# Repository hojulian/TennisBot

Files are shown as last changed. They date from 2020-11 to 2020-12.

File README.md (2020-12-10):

# TennisBot

**Julian Ho, Cass Wang**

**COSI 119A Fall 2020**

TennisBot AR

TennisBot is a tennis playing robot capable of playing a full tennis match.

## Final Report

[Github Pages](https://hojulian.github.io/TennisBot)

## Directory Structure

* `/docs` - final report, github pages
* `/docs/images` - images of the project
* `/firmware` - all firmware/configs for MCU, motor ESCs, and actuator
* `/hardware` - BOM, 3D printed parts files
* `/lib/quickshot` - QuickShot library
* `/models/designs` - 3D design source files
* `/models/gazebo` - 3D models in gazebo
* `/reports` - weekly reports
* `/tools` - snapshot of the tools for ESC configuration

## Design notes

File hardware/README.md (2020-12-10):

# Hardware

## 3D prints

All included STL files are optimized for printing using a Ender 3 V2 printer.

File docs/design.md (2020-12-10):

# Design

TennisBot AR

## Overview

When designing the TennisBot v1, we gave ourselves a couple hard requirements,

1. Capable of shooting a professional shot (~70 mph speed, ~3000 rpm spin)
2. Can shoot a ball to any position of the court, +/- 5cm tolerance
3. Battery powered
4. Portable

With these limitations, we had to constraint and revise our design a lot.

(1) and (2) depends on our motor selection, we needed motors that can reach >10,000 rpm while being relatively lightweight. Therefore we picked a 3548 BLDC motor, which is capable of reaching 19,980 rpm at 22.2v, at 150g a piece. At our maximum requirement of 8500 rpm, this motor will draw ~35A which is acceptable for our use case. In order to accurately land a ball, we need fine control of the shooter's angle. We picked a large 9235 BLDC motor, combined with an AS5047p 14bit absolute magnetic encoder, that gives us a fine grained angle control of 0.02 degrees.

(3) is relatively easy constraint since the modern LiPo batteries can have a high power output while being portable (commonly used in RC cars and drones). We designed the whole robot to be DC powered, and can be charged with a portable power adapter.

(4) created constraint on the physical weight and size of the robot. We designed the robot to have a small footprint (less than the size of a pizza box), and light enough to be carried with a suitcase (~ 10Kg total).

## Changes along the way

During the physical testing of our design, we realized a couple things that needed to be changed.

* Actuator not powerful enough to hold shooter's angle
  * Solution: changed motor from 7032 to a larger 9235
* Belt is too loss/shaky during operation
  * Solution: added 2 idlers, 1 for each motors
* Belt sometimes scratches the carbon fiber plate
  * Solution: changed to narrower belts (12mm -> 10mm width) and also a narrower gear to keep the belt in position (Idlers helped with this as well)
* Not enough friction between the 2 wheels and the tennis ball
  * Solution: changed to larger wheels (83mm -> 90mm diameter) to have a larger contact area with the ball, and compress the ball more during shots
* Encoder producing noisy signal
  * Solution: used shielded cables instead to protect the signal from motors' EMI

## 3D Modelling

TennisBot is designed using Shapr3D. All the source design files can be found under [/models/designs](../models/designs).

Here are some images of TennisBot v1 in 3D and AR.

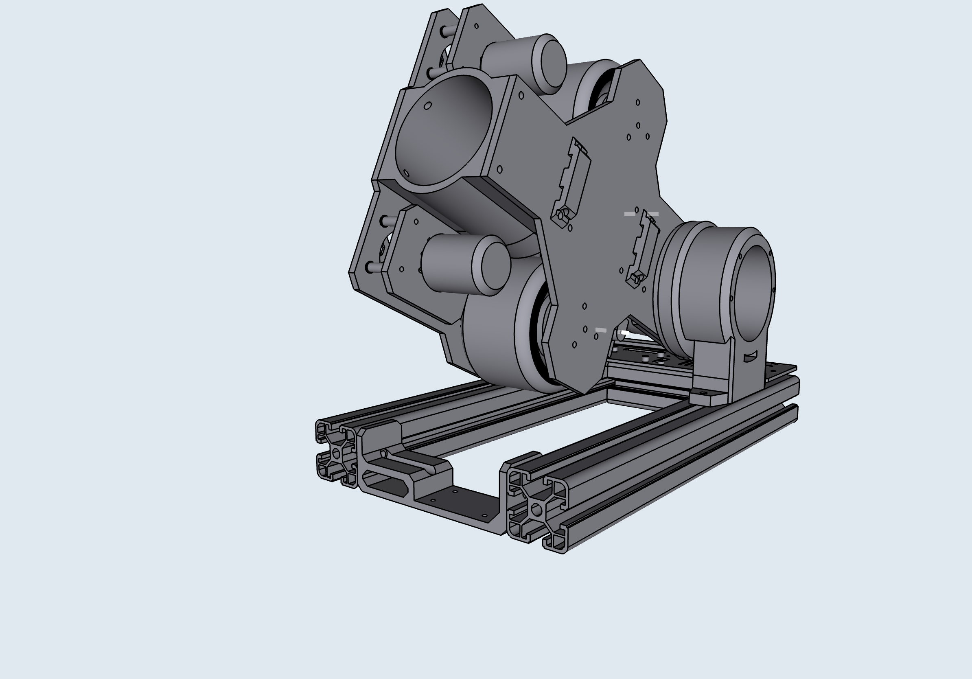
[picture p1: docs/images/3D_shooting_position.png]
3D shooting position


*Shooter at 30 degrees shooting position*

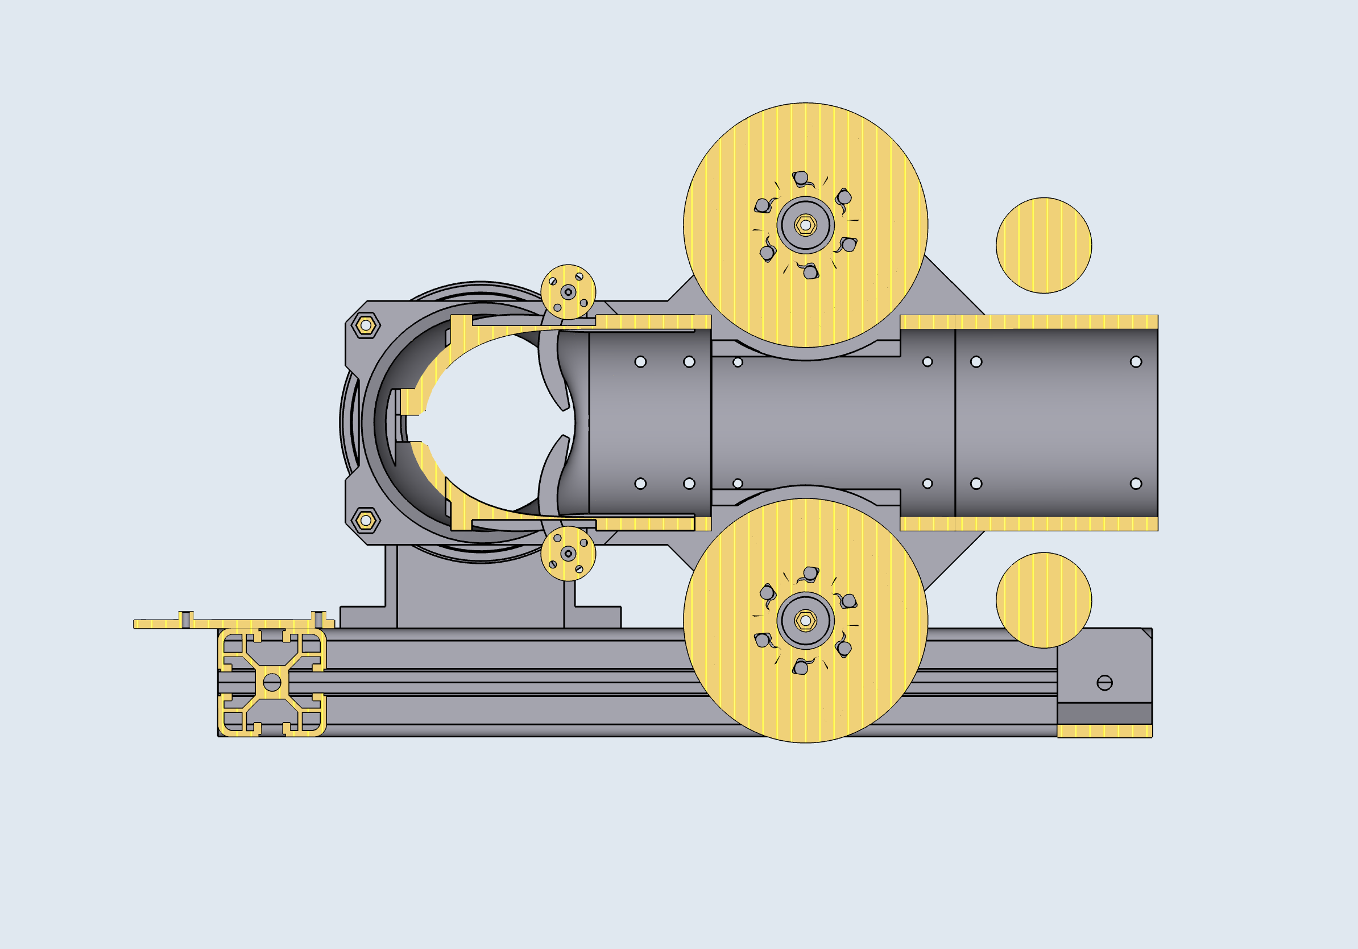
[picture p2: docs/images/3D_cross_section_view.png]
3D cross section


*Cross section of the shooter pipe*

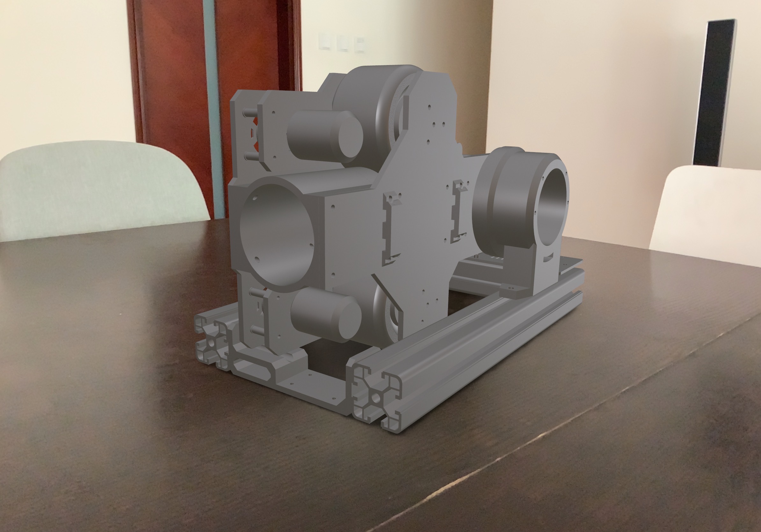
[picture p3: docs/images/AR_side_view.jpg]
AR side view


*Apple AR view*

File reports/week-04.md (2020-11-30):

# TennisBot - Week 4 report

Julian Ho, Cass Wang

## In progress

* Implement firmware for driving tennis shooter hardware using ESP32 (Julian)
* Continue testing URDF implementation in Gazebo (Julian)
* Standardize/clean up ball shooting python library (Cass)

## Completed

* Hardware assembly of the tennis shooter (Julian)
* Initial implementation of the ball shooting library (Cass)

## Planned for next week

* Test out ball shooting library in Gazebo (Julian)
* Building the tennis court in Gazebo (Cass)

## Demo

* Ball launching with dual motors

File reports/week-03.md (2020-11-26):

# TennisBot - Week 3 report

Julian Ho, Cass Wang

## In Progress

* Implement ball shooting algorithms in Python (Cass)
* Test URDF in gazebo and add controls (Julian)
* Building a tennis court in gazebo (Cass)

## Completed

* Convert tennis shooter into URDF (Julian)
* 3D print components to check fit and finish (Julian)

## Planned for next week

* URDF Testing (Julian)
* Finish implementation of ball shooting algorithms in Python (Cass)

## Demo

* Trigger control
* Working URDF model in gazebo

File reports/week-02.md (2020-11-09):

# TennisBot - Week 2 report

Julian Ho, Cass Wang

## In Progress

* Convert tennis shooter into URDF (Julian)
* 3D print components to check fit and finish (Julian)
* Building a tennis court in gazebo (Cass)

## Completed

* Finalize tennis shooter 3D design (Julian)
* Create github repo for the project (Julian)
* Research for ball shooting algorithms (Cass)

## Planned for next week

* Continue building tennis court in gazebo (Cass)
* Convert tennis shooter into URDF (Julian)
* Demo the trigger part of the tennis shooter (Julian)

## Demo

* 3D printed components of the tennis shooter
* Tennis shooter in AR

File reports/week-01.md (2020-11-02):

# Week 1 report

## In Progress

* Finalizing the ball shooter assembly in 3D (Julian)
* Research for building out a tennis court in Gazebo (Cass)

## Completed

* Create github repo for the project (Julian)
* Research for ball shooting algorithms (Cass)

## Planned for next week

* Start building a tennis court in Gazebo (Cass)
* Convert ball shooter assembly to URDF (Julian)

## Demo

* First draft of the TennisBot in 3D
* A [paper](http://www.actawm.pb.edu.pl/volume/vol5no4/WOJCICKI_KULESZA_PUCILOWSKI_EN_2010_085.pdf) regarding ball shooter calculations for ball shooter

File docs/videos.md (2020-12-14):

# Video Demos

* [3D overview](https://drive.google.com/file/d/1ATR15ysar9NvpiEGBQoBEaimcxwtdzJY/view?usp=sharing)
* [Motors control]()
* [Actuator control](https://drive.google.com/file/d/1KERbm8YpcWQQ3XklB0WpKhzmQzhS0fMN/view?usp=sharing)
* [Tennis Court in gazebo](https://drive.google.com/file/d/1kdG3kgPG80MRxjjYmwbdfLqyGcjW15ck/view?usp=sharing)
* [TennisBot V1 in RViz](https://drive.google.com/file/d/1K_xSpBqOkkCilqj5o8Mh0_ldypU9PAPF/view?usp=sharing)

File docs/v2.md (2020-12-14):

# V2 and Beyond

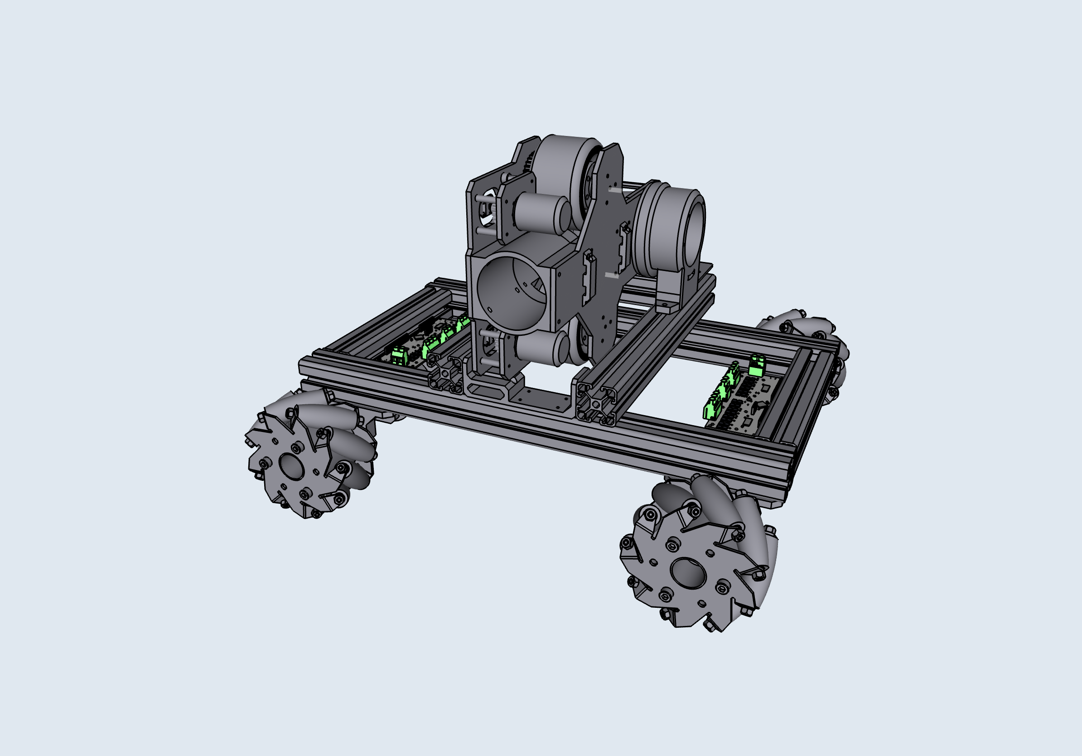
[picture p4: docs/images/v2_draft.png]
TennisBot v2 Draft


The eventual goal for this project is to have a fully automated robot for playing a full tennis match.

## V2 Changes

* A chassis will be added, driven by 4 omni-directional wheels each with an individual motor.
* QuickShot library will support target in `x` direction as well.

    ```python
    # Shoot the ball 1 meter to the left and 2 meters up front.
    q.calc_params(
      y=200,
      x=-100,
      # ...
    )
    ```

* A stereo depth camera on-board for trajectory prediction, in order for the robot to "return" the ball.
* The v2 robot does not actually return the ball in the traditional sense, instead, it moves to where the ball is suppose to land and shoots a ball back immediately.

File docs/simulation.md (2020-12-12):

# Simulation

In order to test out the robot, we exported the 3D model into gazebo, along with a custom built testing ground.

All source files are in [/models/gazebo](../models/gazebo).

## TennisBot v1

In order to keep our simulation simple and smooth, we exported a simplified version of the TennisBot using solidworks' URDF exporter. This simplified verion has a simple geometry while maintaining the exact dimensions of the robot.

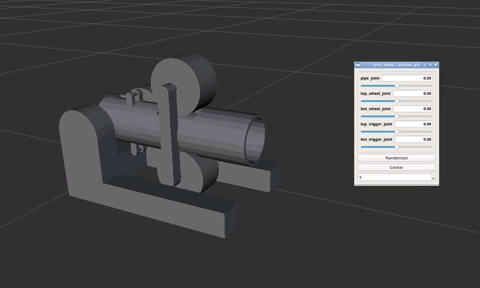
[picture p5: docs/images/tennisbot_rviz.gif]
tennisbot rviz


*^Here it is running in RViz*

This model has a total of 5 joints,

* 1 joint for tilt control
* 1 joint per wheel
* 1 joint per trigger

Each joint can be independently controlled (as shown above).

All the source files can be found in [/models/gazebo/tennisbot_support](../models/gazebo/tennisbot_support).

### Launch in RViz

```bash
roslaunch tennisbot_support display.launch
```

### Launch in Gazebo

```bash
roslaunch tennisbot_support gazebo.launch
```

## Tennis Court

In order to test out our robot design, we first created a tennis court in Blender, then exported it to URDF for use in gazebo.

tennis court blender

*^The red object is our robot*

### Gazebo world

```bash
/models/gazebo/tennis court/Tennis_Court.world
```

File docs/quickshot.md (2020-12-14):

# QuickShot - Tennis Shooting Algorithm

We have created a Python library (QuickShot) for calculating the exact parameters needed for landing a ball to a given location at a given speed/spin using TennisBot v1.

All the calculations/equations here are modified based on this [paper](http://www.actawm.pb.edu.pl/volume/vol5no4/WOJCICKI_KULESZA_PUCILOWSKI_EN_2010_085.pdf).

Our detailed explanations of the implementation of the paper [here](shooting_algorithm.pdf).

## Usage

```python
# Initiate shooter with the robot's physical capabilities
q = quickshot.Shooter(
  min_rpm=400,
  max_rpm=8400,
  min_angle=0,  # min/max angle in degrees
  max_angle=80,
)

# Calculate the parameters needed for shooting the ball.
params = q.calc_params(
  y=200,  # distance (cm) from the robot
  speed=20,  # speed in meters per second
  top_spin=0, # top/back spin in meters per second
  back_spin=0,
)

# Prepare the shooter (spinning up the motors) for the shot.
shooter.prepare(
  top=params['top_motor'],
  bottom=params['bottom_motor'],
  angle=params['angle'],
)

shooter.shot_once_ready()
```

All the source code for QuickShot is located in [/lib/quickshot](../lib/quickshot).

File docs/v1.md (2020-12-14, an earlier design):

# TennisBot v1

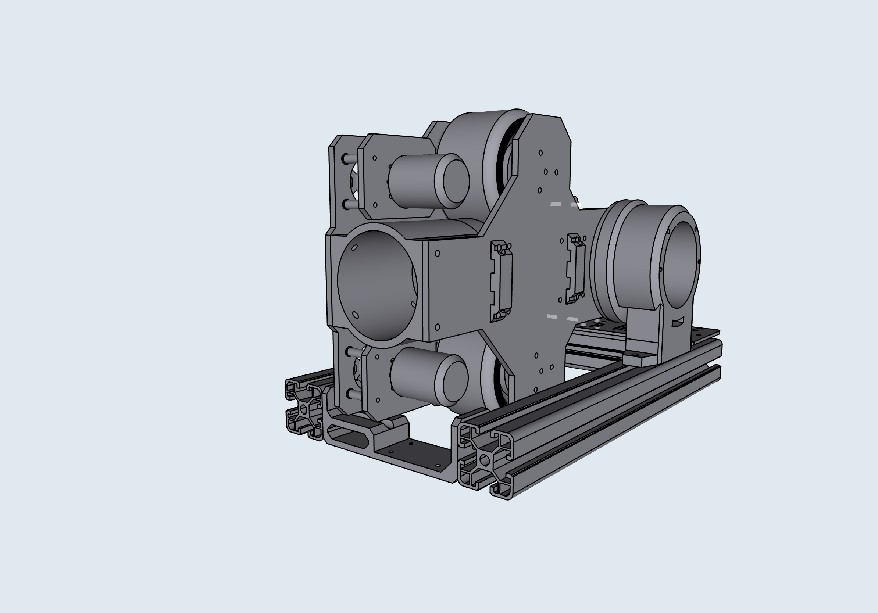
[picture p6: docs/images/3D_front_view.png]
TennisBot v1


TennisBot v1 is a tennis playing robot that can serve balls at a fixed location. It has tilt, top/back spin, as well as ball frequency control. It is capable of shooting the ball at 40 m/s^ (or 89.5 mph) and spin of 8490 rpm^.

*^Theoretical highest speed, based on the selected motor and power output*

## Features

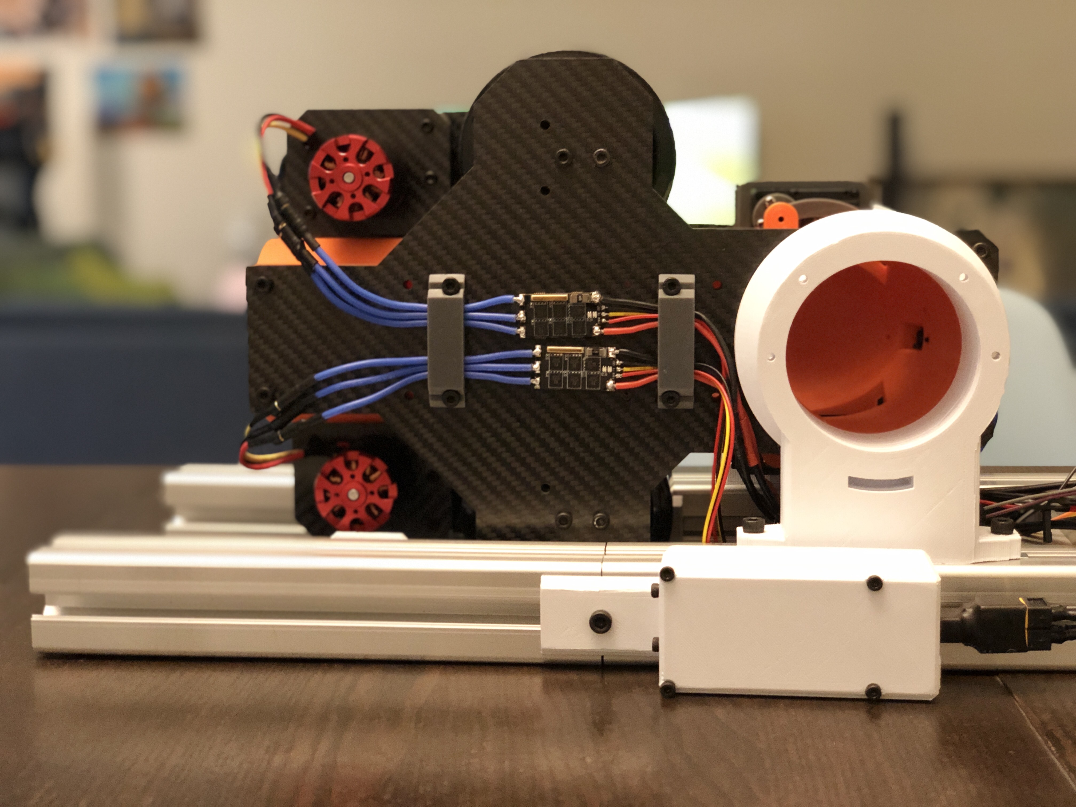
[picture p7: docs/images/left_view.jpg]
Left view


* 40 m/s top ball speed
* 8490 max ball RPM
* battery powered

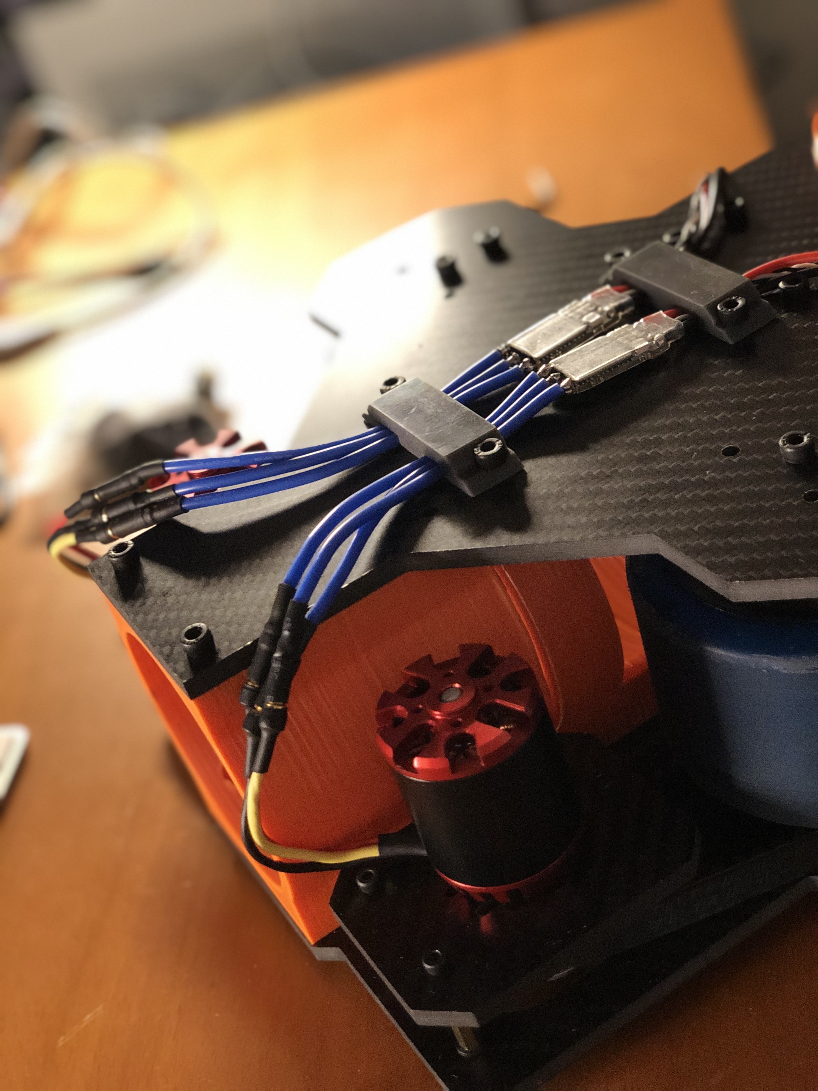
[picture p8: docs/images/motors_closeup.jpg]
Motors closeup


* 2 BLDC motors powered by 2 lightweight ESCs
* 1670W of raw motor power
* 2:1 gear ratio
* 90mm wheels

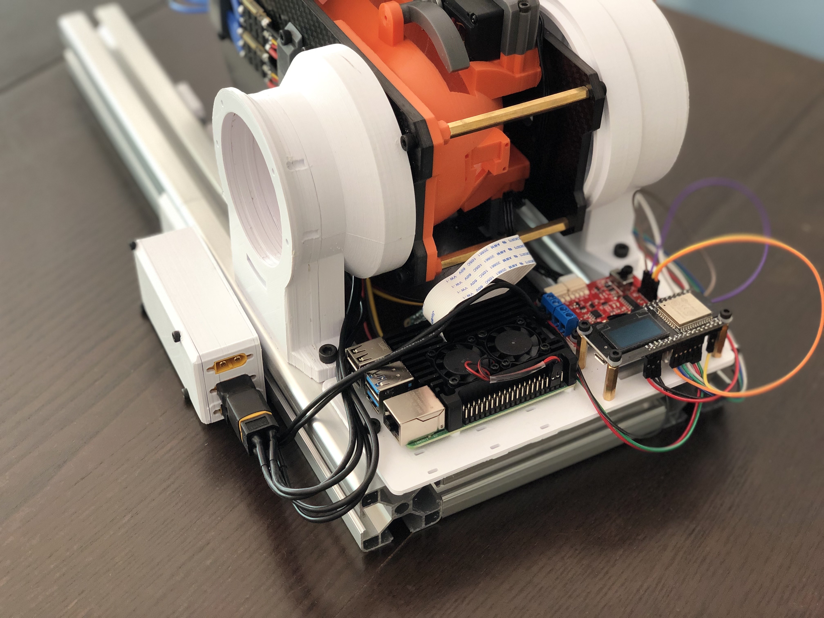
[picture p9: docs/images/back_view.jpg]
Back view


* RPi 4 running ROS melodic
* ESP32 for hardware control
* Communicate using over serial via USB using rosserial

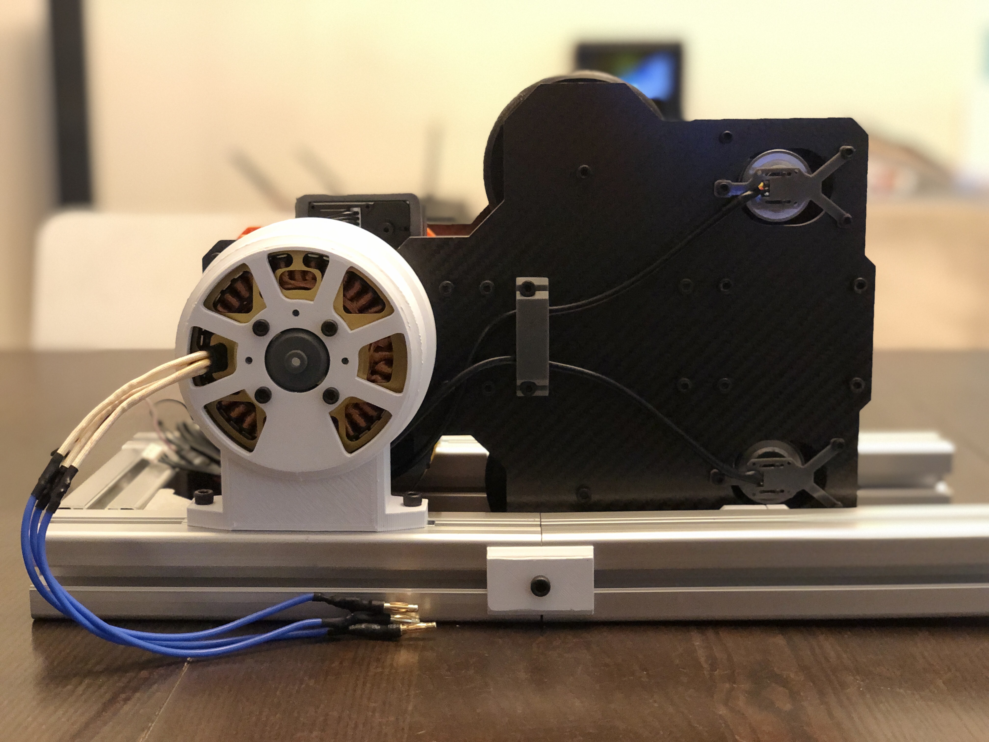
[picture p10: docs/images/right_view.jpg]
Right view


* Dual 14bit magnetic encoders (for RPM tracking)

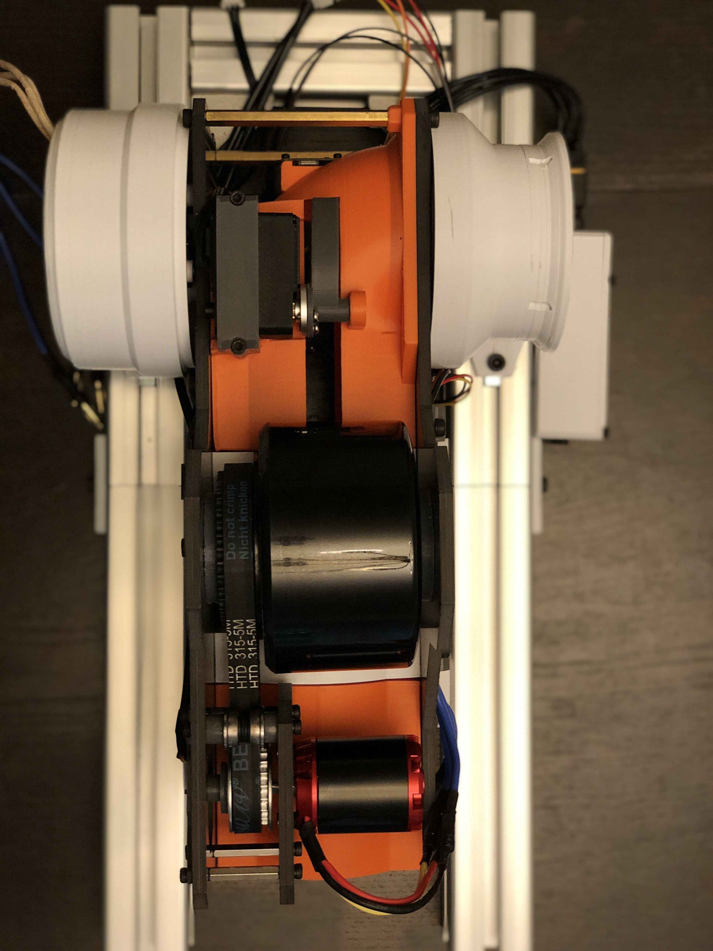
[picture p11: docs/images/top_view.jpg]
Top view


* Belt driven drive
* 2:1 reduction ratio
* Idler for better stability at high RPM

## Design

See [Design](design.md).

## V1 Limitations

This version of TennisBot is not capable of playing a full tennis match just yet, since it only includes the shooter component. However, the shooter component allows us to practice returns, and some tennis drills.

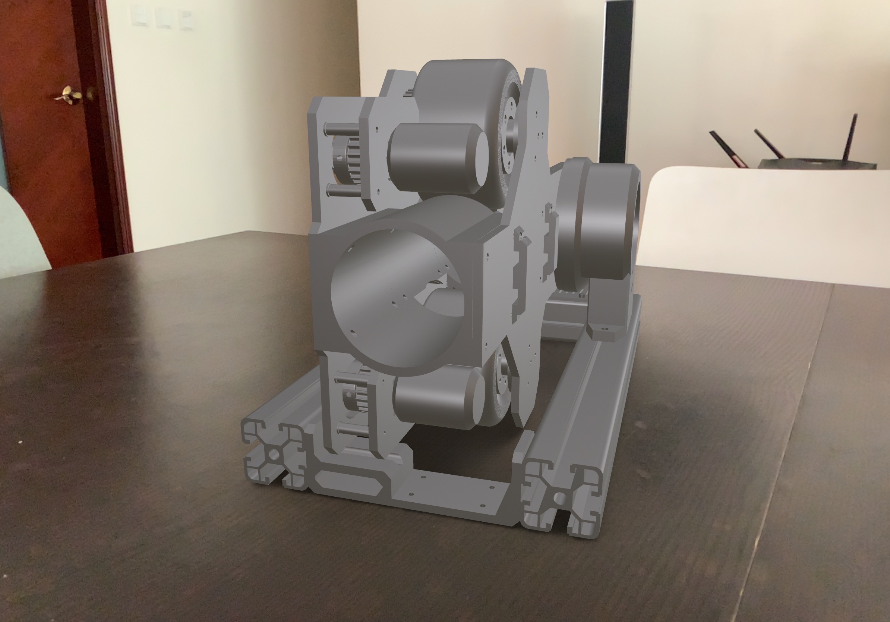
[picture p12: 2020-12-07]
docs/images/AR_front_view.jpg

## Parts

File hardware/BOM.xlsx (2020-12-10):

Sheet: TennisBot v1
TennisBot v1
Product Name | Quantity | Unit Price in USD (As of Nov '20) | Total
ST3215 Servo | 2 | $13.50 | $27.00
URT-1 servo control board | 1 | $6.00 | $6.00
Wraith32 V2 BLDC Controller | 2 | $15.75 | $31.50
N3548 900KV BLDC motor | 2 | $12.94 | $25.87
W9235 BLDC motor | 1 | $25.50 | $25.50
Odrive 3.6 56V BLDC controller | 1 | $69.00 | $69.00
AS5047P encoder | 1 | $9.90 | $9.90
AS5048A encoder | 2 | $8.82 | $17.64
ESP32 WROVER-B | 1 | $7.16 | $7.16
Raspberry Pi 4B 4GB | 1 | $55.00 | $55.00
4040 metal beam (35cm x2, 22cm x1) | 1 | $3.00 | $3.00
Abec 7 90mm wheels | 2 | $7.50 | $15.00
M4 16mm screws (50 pcs) | 1 | $0.45 | $0.45
M4 8mm screws (50 pcs) | 1 | $0.45 | $0.45
M3 12mm screws (50 pcs) | 1 | $0.45 | $0.45
M3 8mm screws (50 pcs) | 1 | $0.45 | $0.45
M2.5 5mm screws (50 pcs) | 1 | $0.45 | $0.45
M2 5mm screws (50 pcs) | 1 | $0.45 | $0.45
M4 hex metal beam 80mm (10 pcs) | 1 | $2.64 | $2.64
M3 hex metal beam 25mm (10 pcs) | 1 | $0.45 | $0.45
75mm ID 95mm OD bearing | 1 | $4.50 | $4.50
F687ZZ bearing | 4 | $0.33 | $1.32
AMASS XT60 Female connector | 4 | $0.28 | $1.14
AMASS XT60E-M connector | 4 | $0.31 | $1.23
18T 5mm ID HTD5 pulley | 2 | $2.70 | $5.40
 |  |  |  | $311.96
 |  |  | Total | $311.96

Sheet: TennisBot v2
TennisBot v2
Product Name | Quantity | Unit Price in USD (As of Nov '20) | Total
4 ports powered USB 3.0 hub | 1 | $12.75 | $12.75
Intel Realsense D455 | 1 | $245.00 | $245.00
 |  |  |  | $257.75
Odrive 3.6 56V BLDC controller | 2 | $73.50 | $147.00
N5055 330KV BLDC motor | 4 | $22.50 | $90.00
6200mAh 3S 35C LiPo battery | 4 | $19.20 | $76.80
ASSAN Dual-UBEC power module | 1 | $12.75 | $12.75
iFlight Succex PDB | 2 | $10.35 | $20.70
 |  |  |  | $347.25

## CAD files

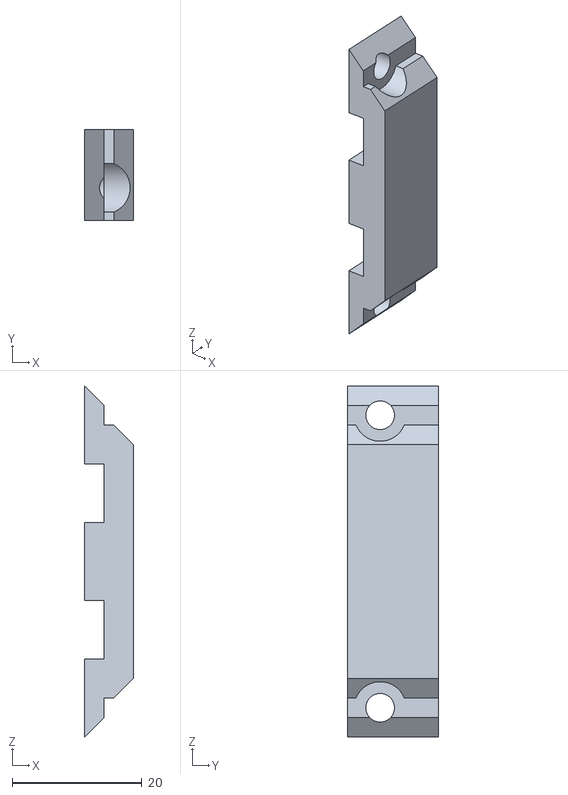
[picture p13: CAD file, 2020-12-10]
hardware/3D prints/cable mount.stl
7.50 x 14.0 x 54.0

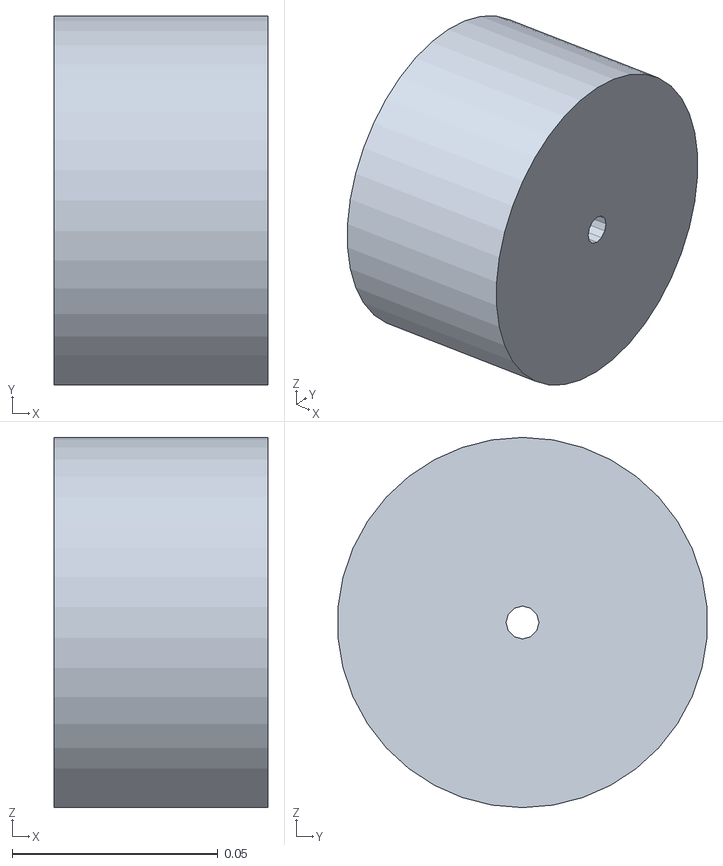
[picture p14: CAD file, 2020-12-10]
models/gazebo/tennisbot_support/meshes/bot_wheel_link.STL
0.052 x 0.0897 x 0.09

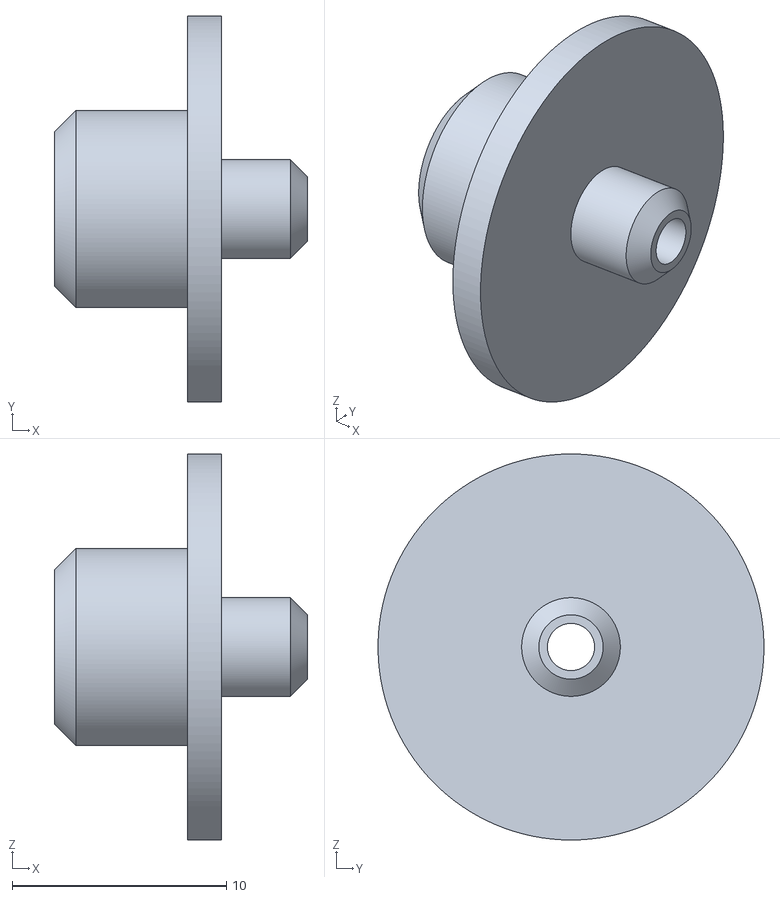
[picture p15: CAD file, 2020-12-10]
hardware/3D prints/gear magnet holder.stl
11.8 x 18.0 x 18.0

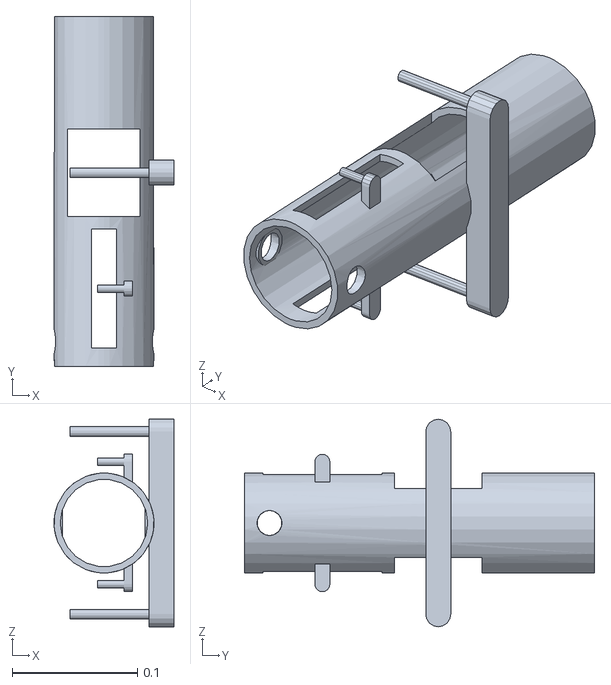
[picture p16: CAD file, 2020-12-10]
models/gazebo/tennisbot_support/meshes/pipe_link.STL
0.096 x 0.28 x 0.166

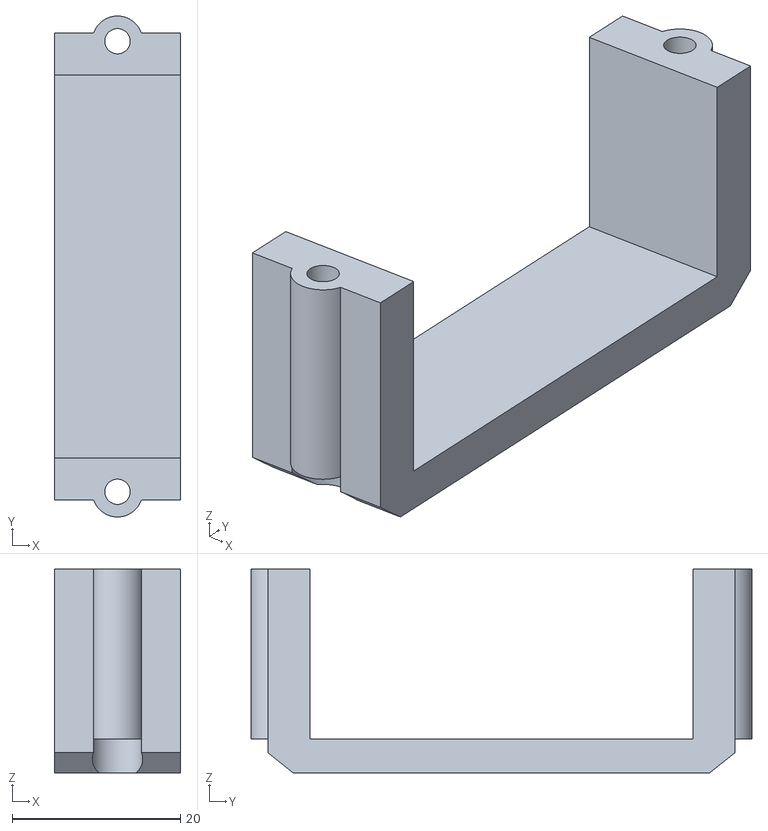
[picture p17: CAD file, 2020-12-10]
hardware/3D prints/shooter servo holder.stl
15.0 x 59.5 x 24.2

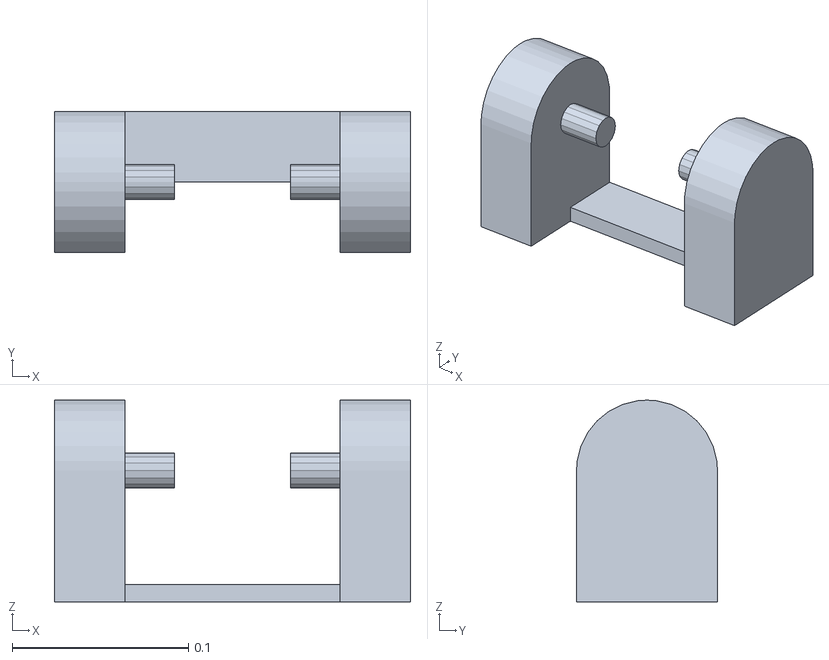
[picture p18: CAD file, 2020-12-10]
models/gazebo/tennisbot_support/meshes/mount_link.STL
0.202 x 0.08 x 0.115

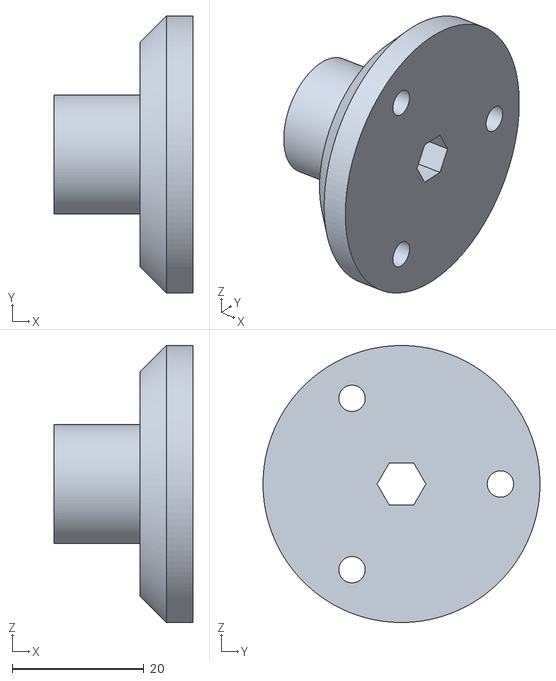
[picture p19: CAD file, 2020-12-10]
hardware/3D prints/wheel holder bottom.stl
21.0 x 42.0 x 42.0

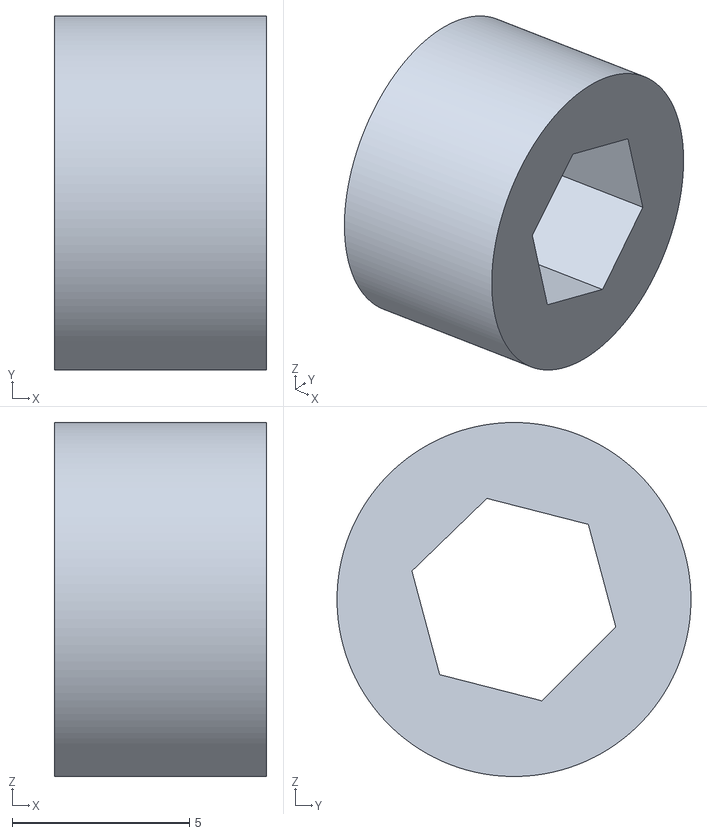
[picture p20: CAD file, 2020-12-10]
hardware/3D prints/idler bottom.stl
6.00 x 10.00 x 10.0

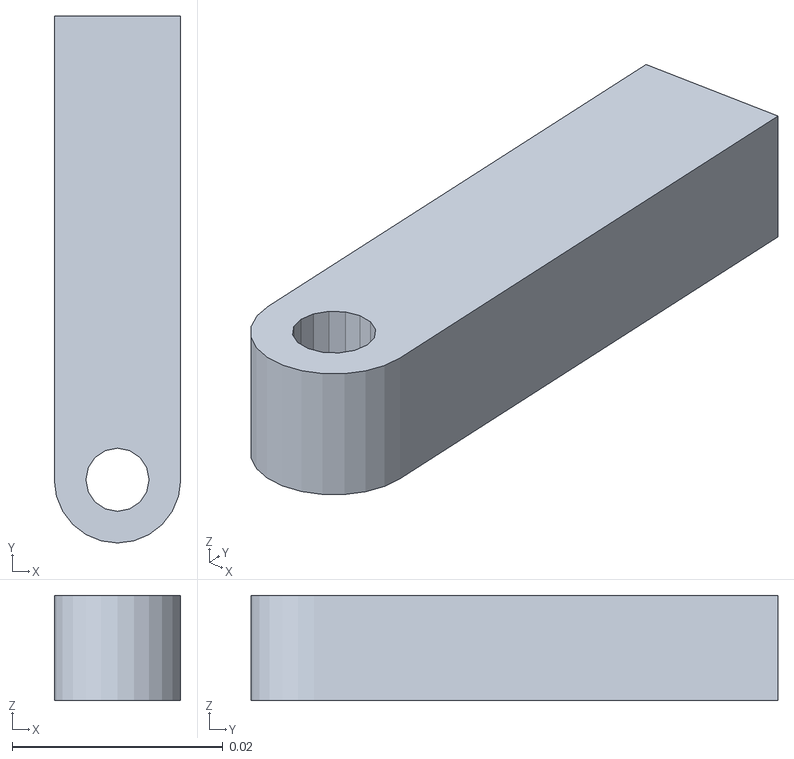
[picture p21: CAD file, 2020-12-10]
models/gazebo/tennisbot_support/meshes/bot_trigger_link.STL
0.012 x 0.05 x 0.01

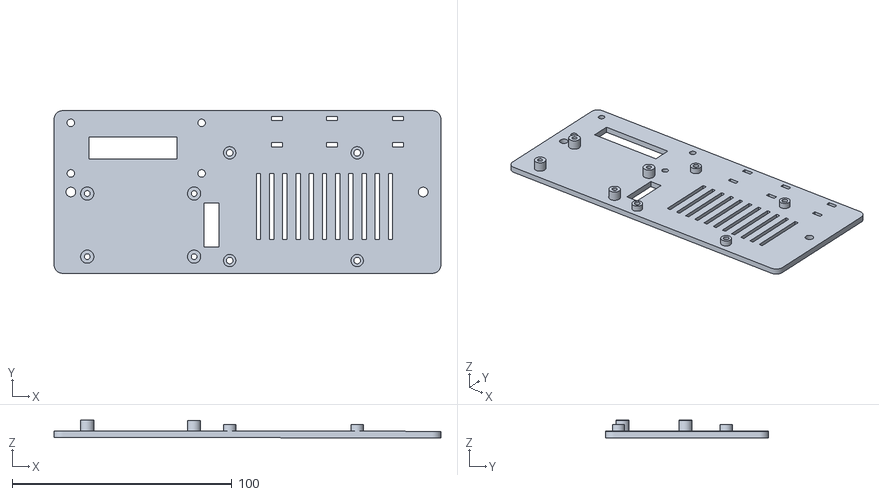
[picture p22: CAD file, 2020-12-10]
hardware/3D prints/test board.stl
176.0 x 74.0 x 8.07

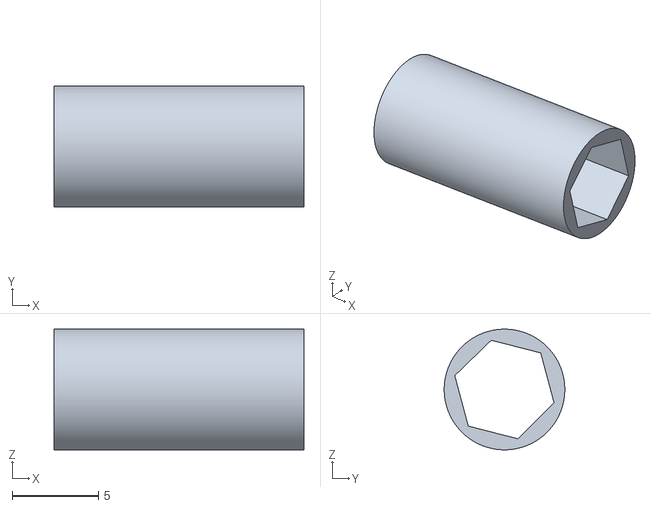
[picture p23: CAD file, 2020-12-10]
hardware/3D prints/idler spacer.stl
14.5 x 7.00 x 7.00

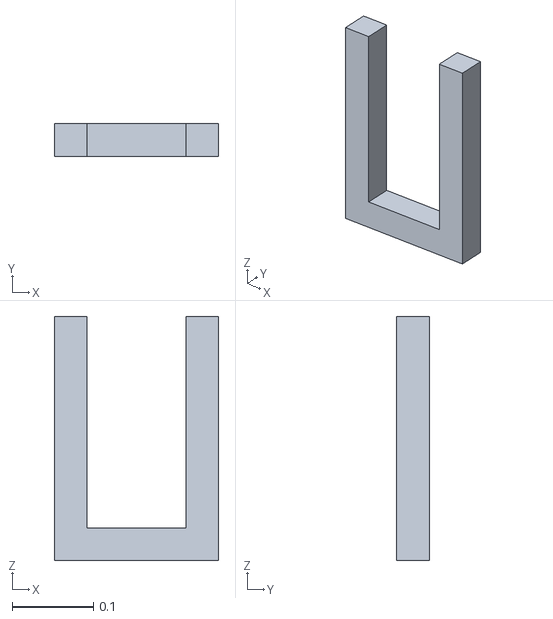
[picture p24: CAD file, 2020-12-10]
models/gazebo/tennisbot_support/meshes/base_link.STL
0.202 x 0.04 x 0.3

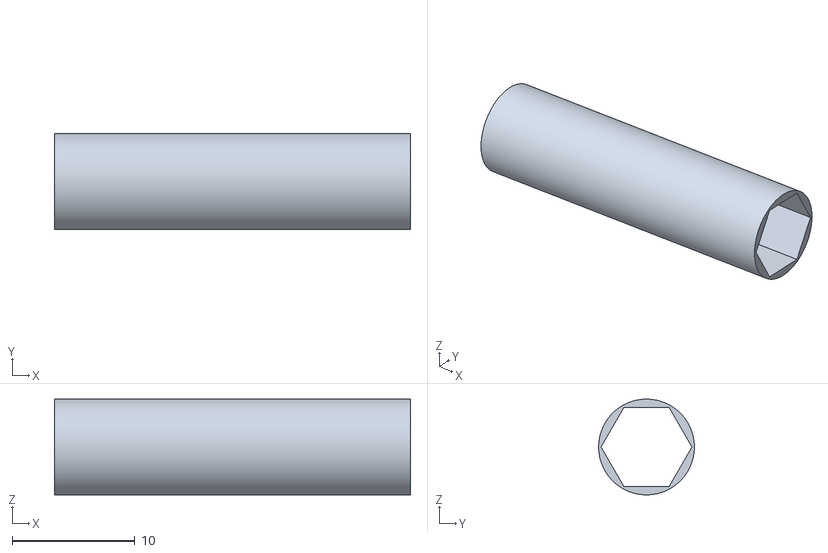
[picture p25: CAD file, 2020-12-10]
hardware/3D prints/wheel spacer.stl
29.0 x 7.80 x 7.80

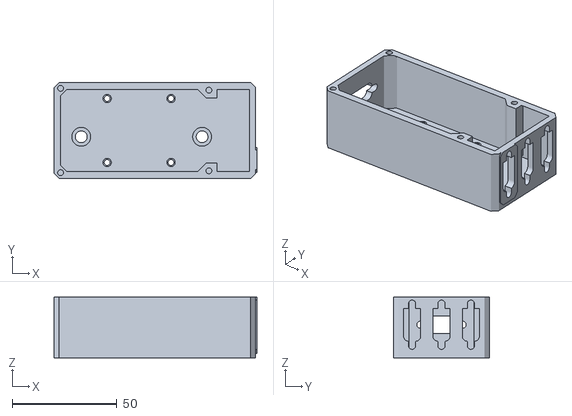
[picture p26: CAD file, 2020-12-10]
hardware/3D prints/power distribution board.stl
96.8 x 46.0 x 29.0

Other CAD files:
models/gazebo/tennisbot_support/meshes/top_wheel_link.STL
models/gazebo/tennisbot_support/meshes/top_trigger_link.STL
hardware/3D prints/actuator housing.stl
hardware/3D prints/actuator magnet cover.stl
hardware/3D prints/actuator encoder cover.stl
hardware/3D prints/actuator plate.stl
hardware/3D prints/front mount.stl
hardware/3D prints/idler top.stl
hardware/3D prints/left mount.stl
hardware/3D prints/power distribution board cover.stl
hardware/3D prints/shooter end pipe.stl
hardware/3D prints/shooter mid pipe.stl
hardware/3D prints/wheel holder top.stl

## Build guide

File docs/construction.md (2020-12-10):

# Robot Construction

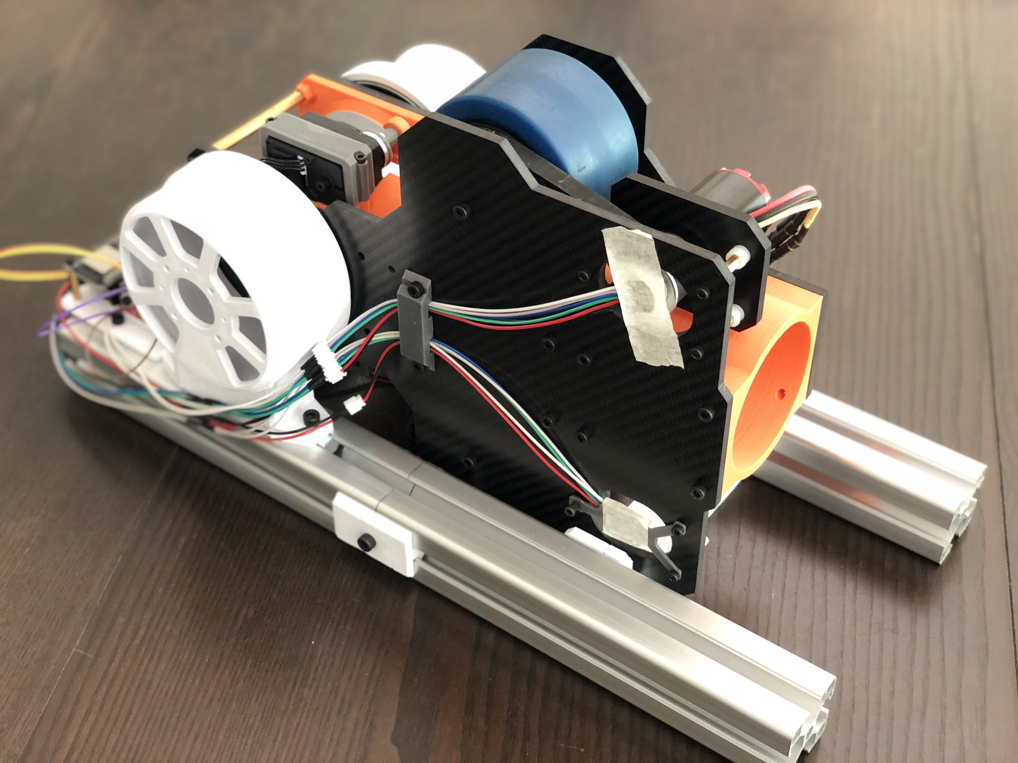
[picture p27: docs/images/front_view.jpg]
TennisBot v1 Front


Since the conception of the TennisBot v1 in 3D, we have been physically building the robot.

*As of December 8th, 2020, all hardware constructions are completed, the remaining work is software tuning.*

## Software Requirements

*For running shooter_controller on ESP32*

* Ubuntu 20.04
* [esptool](https://github.com/espressif/esptool) (for flashing ESP32)
* [odrivetool](https://github.com/madcowswe/ODrive) (for actuator tuning)
* [BLHeliSuite32](https://github.com/bitdump/BLHeli) (for motor tuning)

*For interfacing the ESP32 with ROS on RPi4*

* ROS Melodic
* [rosserial](http://wiki.ros.org/rosserial)

## Hardware Requirements

All material needed to build TennisBot v1 is included in the [hardware](../hardware/BOM.xlsx) folder.

Most the components in the list are off-the-shelf items that can be easily acquired. The only custom parts are the 3D printed components, 4040 metal beams, and the carbon fiber plates.

Basic soldering skill is also required to build this robot.

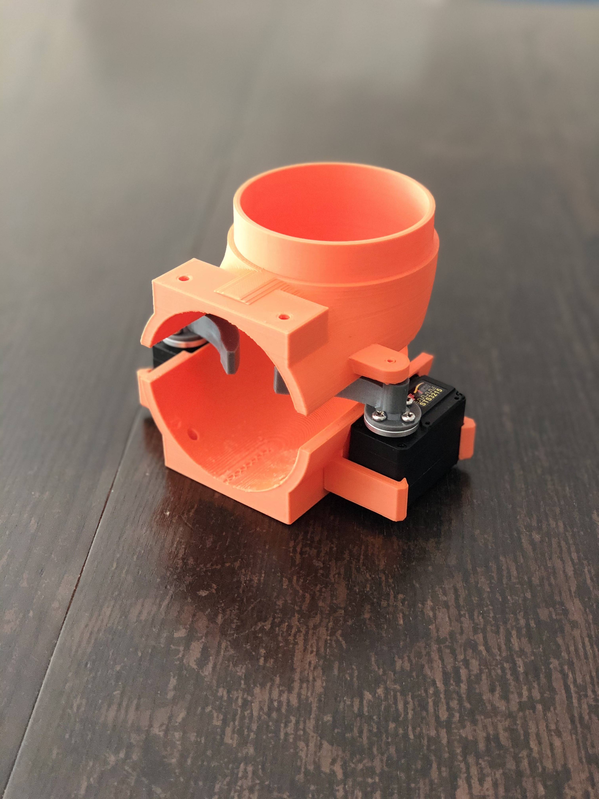
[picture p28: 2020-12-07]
docs/images/trigger_assembly.jpg

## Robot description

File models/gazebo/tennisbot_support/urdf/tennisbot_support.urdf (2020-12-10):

<?xml version="1.0" encoding="utf-8"?>
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
<robot name="tennisbot_support">

  <link name="base_footprint"/>

  <joint name="base_joint" type="fixed">
    <parent link="base_footprint"/>
    <child link="base_link"/>
    <origin xyz="0.0 0.0 -0.162692660283703" rpy="-1.57 0 0"/>
  </joint>

  <link name="base_link">
    <inertial>
      <origin xyz="0.104659789395195 -0.196207572672501 0.162692660283703" rpy="0 0 0" />
      <mass value="1.15520000000003" />
      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
    </inertial>
    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
  </link>
  <link name="mount_link">
    <inertial>
      <origin xyz="4.7805584491023E-10 1.61652830010794E-10 4.26778057338595E-11" rpy="0 0 0" />
      <mass value="0.744243099298161" />
      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
    </inertial>
    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
  </link>
  <joint name="mount_joint" type="fixed">
    <origin xyz="0.104659809442308 -0.266871907624069 0.0733480237700171" rpy="-1.5707963267949 0 -3.14159265358979" />
    <parent link="base_link" />
    <child link="mount_link" />
    <axis xyz="0 0 0" />
  </joint>
  <link name="pipe_link">
    <inertial>
      <origin xyz="0.00896336722335153 0.125428985340103 6.43253882881556E-07" rpy="0 0 0" />
      <mass value="0.33490980168325" />
      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
    </inertial>
    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
  </link>
  <joint name="pipe_joint" type="continuous">
    <origin xyz="0 -0.00131139551645104 0.0238356650484354" rpy="0 0 3.14159265358979" />
    <parent link="mount_link" />
    <child link="pipe_link" />
    <axis xyz="1 0 0" />
  </joint>
  <link name="top_wheel_link">
    <inertial>
      <origin xyz="-0.00100002004712066 1.11022302462516E-16 0" rpy="0 0 0" />
      <mass value="0.328195901335219" />
      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
    </inertial>
    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
  </link>
  <joint name="top_wheel_joint" type="continuous">
    <origin xyz="0 0.135000000000007 0.0729999999999982" rpy="0 0 0" />
    <parent link="pipe_link" />
    <child link="top_wheel_link" />
    <axis xyz="1 0 0" />
  </joint>
  <link name="bot_wheel_link">
    <inertial>
      <origin xyz="-0.00100002004712063 1.11022302462516E-16 -2.77555756156289E-17" rpy="0 0 0" />
      <mass value="0.328195901335218" />
      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
    </inertial>
    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
  </link>
  <joint name="bot_wheel_joint" type="continuous">
    <origin xyz="0 0.135000000000007 -0.0730000000000018" rpy="0 0 0" />
    <parent link="pipe_link" />
    <child link="bot_wheel_link" />
    <axis xyz="1 0 0" />
  </joint>
  <link name="top_trigger_link">
    <inertial>
      <origin xyz="4.69069227904129E-15 0.0206229180482504 -2.00471154815363E-08" rpy="0 0 0" />
      <mass value="0.00556274333882309" />
      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
    </inertial>
    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
  </link>
  <joint name="top_trigger_joint" type="continuous">
    <origin xyz="0 0.0423000000000067 0.0489999999999982" rpy="-1.57079632679491 0 -1.5707963267949" />
    <parent link="pipe_link" />
    <child link="top_trigger_link" />
    <axis xyz="0 0 1" />
  </joint>
  <link name="bot_trigger_link">
    <inertial>
      <origin xyz="3.66373598126302E-15 0.0206229180482504 -2.00471244188316E-08" rpy="0 0 0" />
      <mass value="0.00556274333882308" />
      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
    </inertial>
    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
  </link>
  <joint name="bot_trigger_joint" type="continuous">
    <origin xyz="0 0.0423000000000067 -0.0490000000000018" rpy="1.57079632679488 0 1.5707963267949" />
    <parent link="pipe_link" />
    <child link="bot_trigger_link" />
    <axis xyz="0 0 1" />
  </joint>
</robot>

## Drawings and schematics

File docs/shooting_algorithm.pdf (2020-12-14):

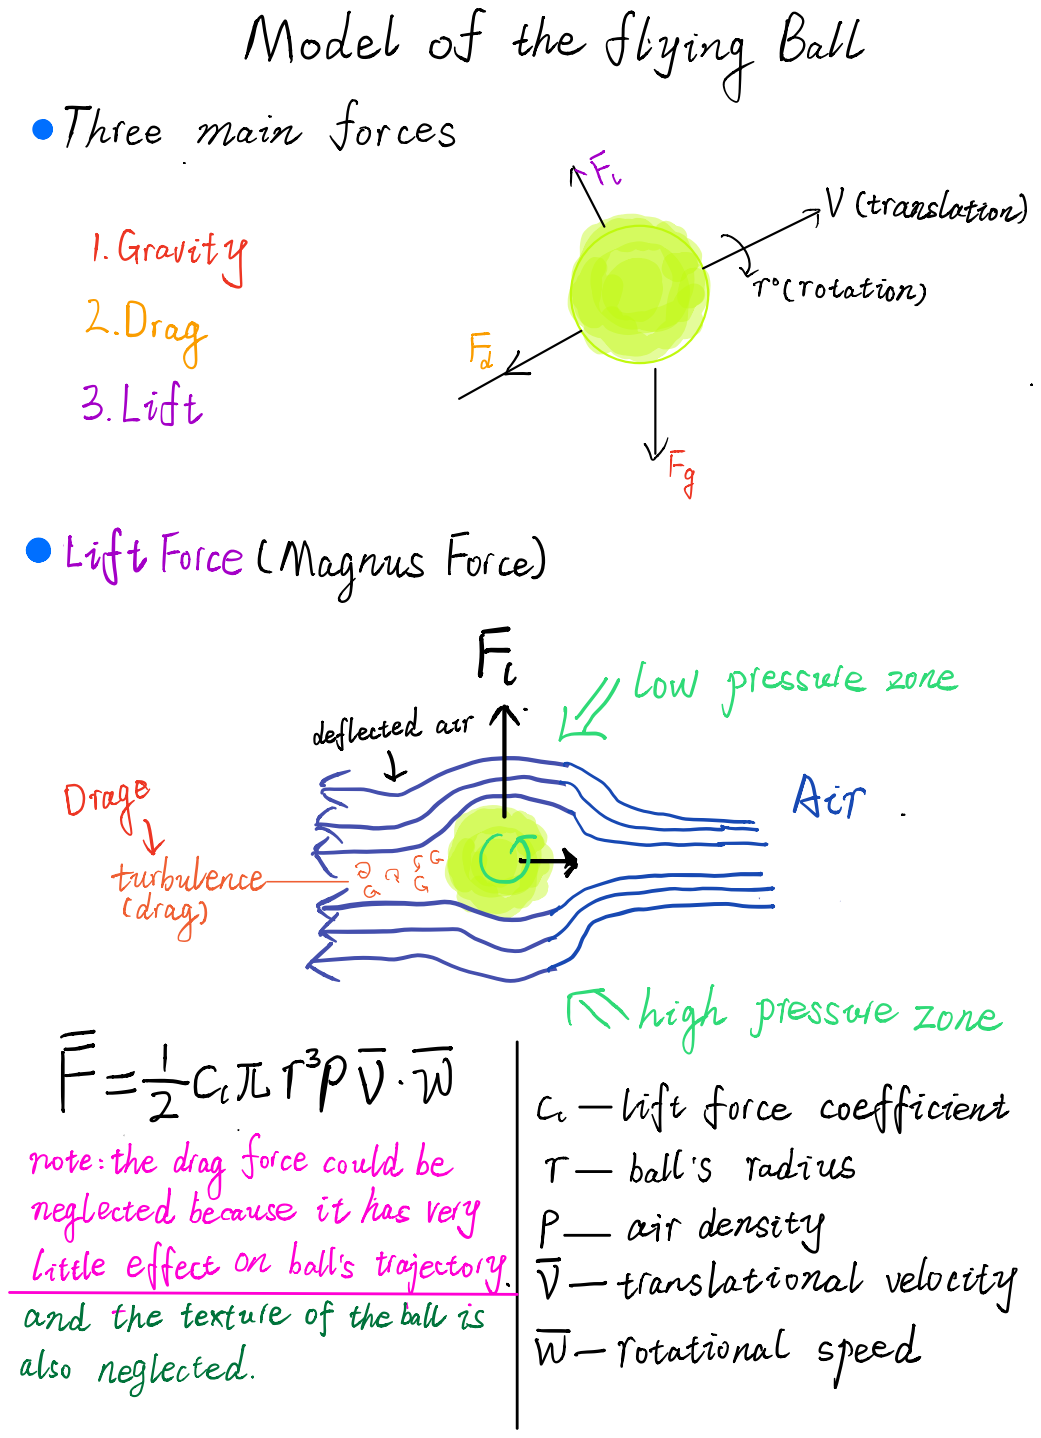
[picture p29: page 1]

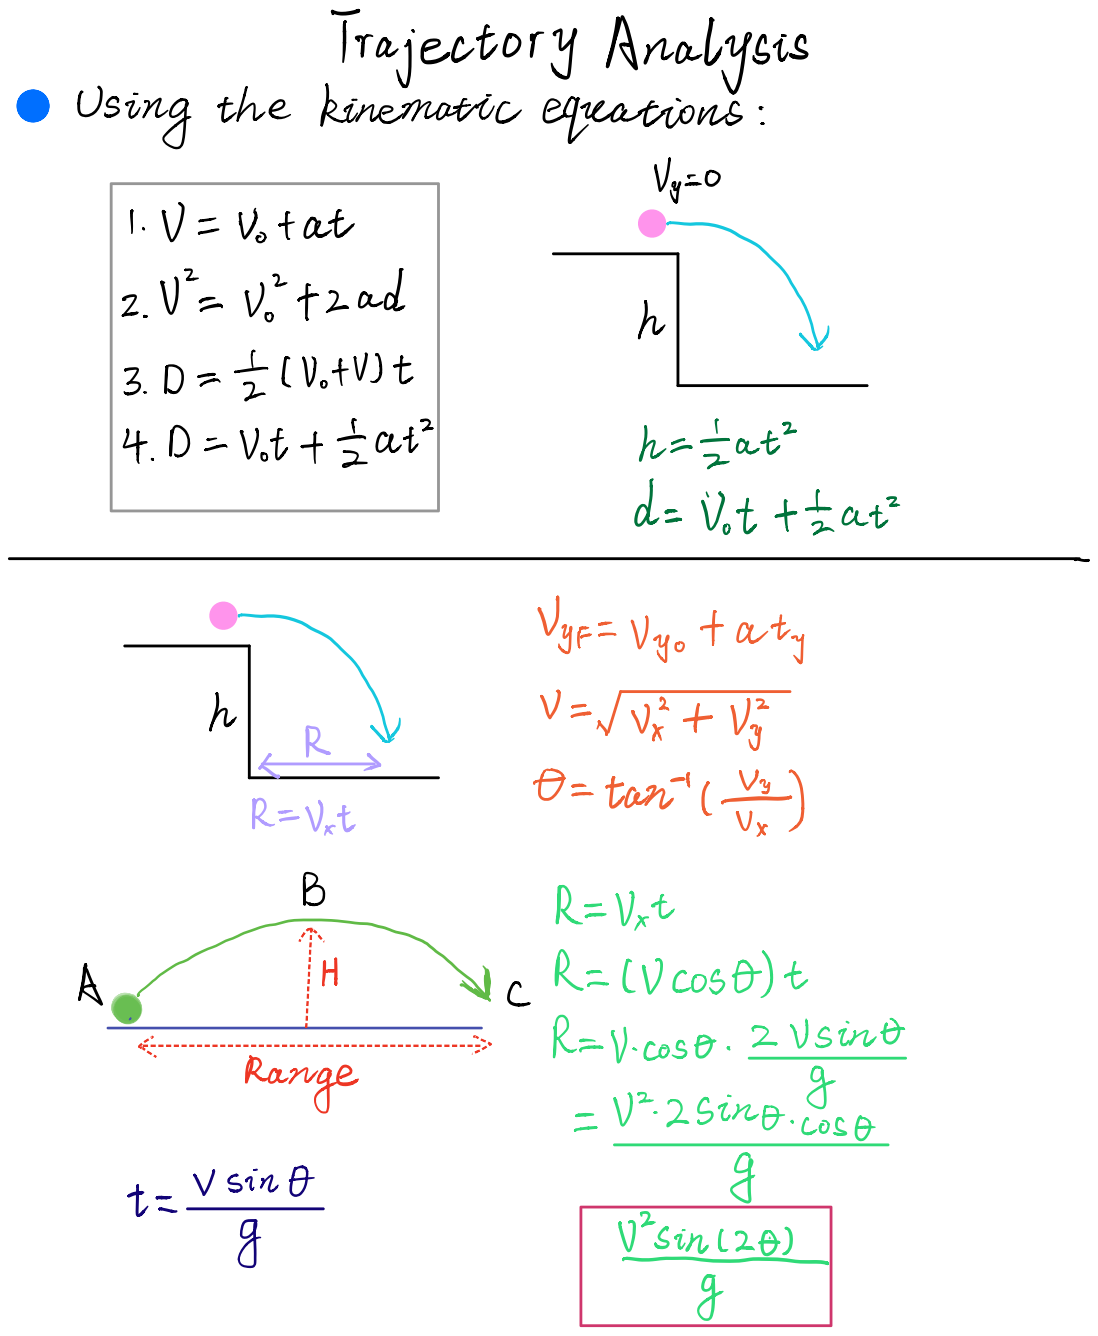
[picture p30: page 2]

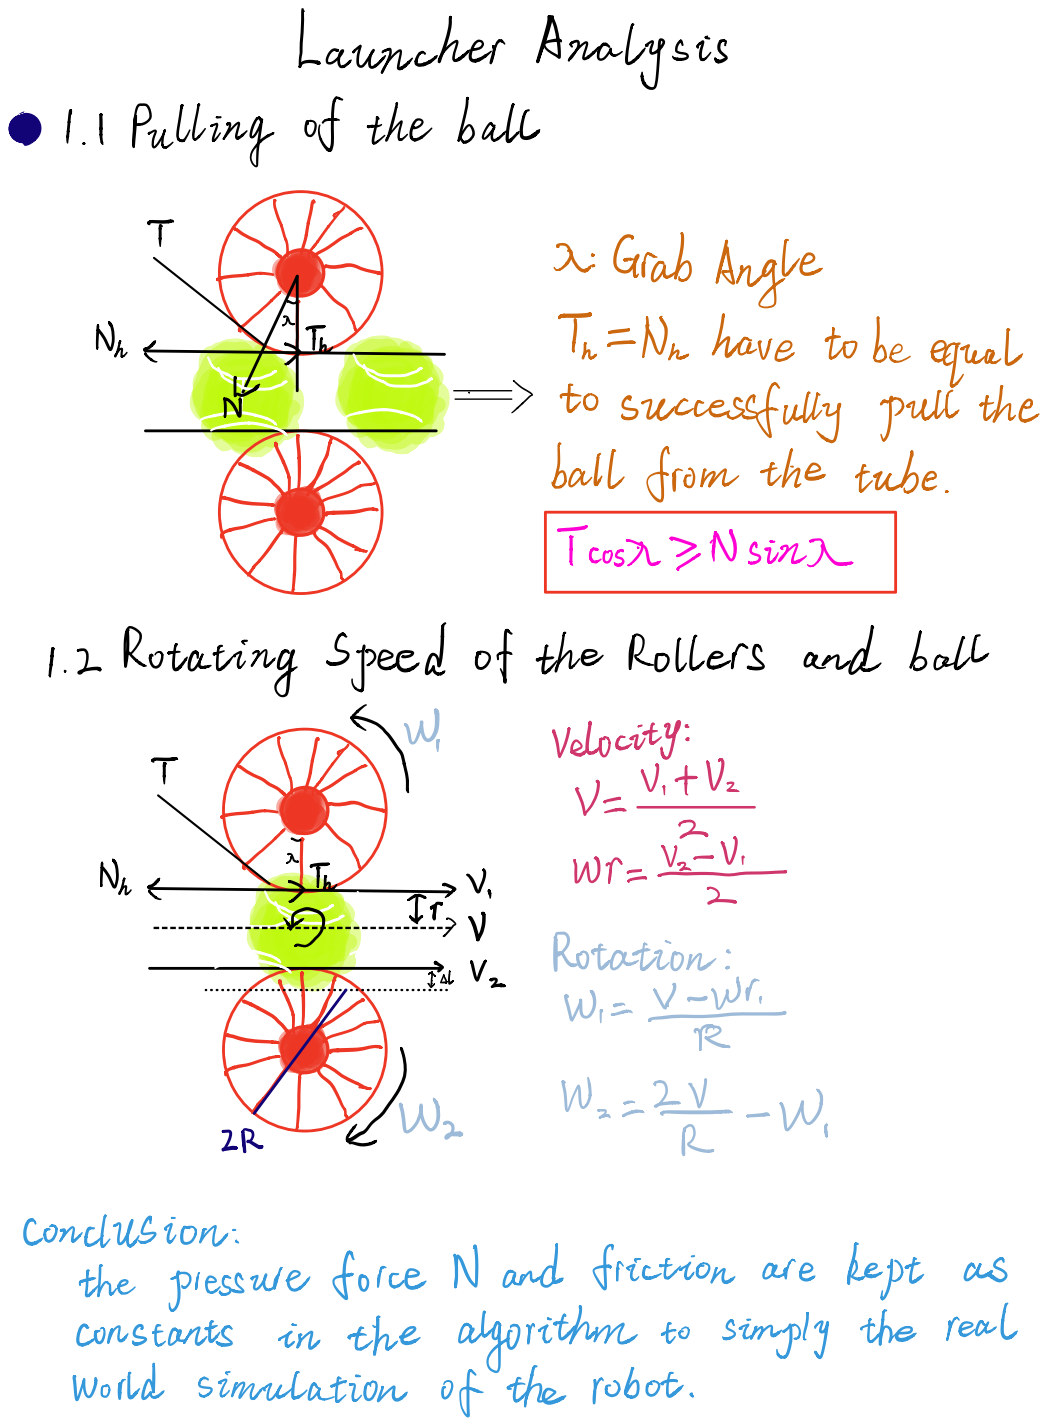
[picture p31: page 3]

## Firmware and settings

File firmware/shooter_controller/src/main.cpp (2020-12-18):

#include <Arduino.h>
#include <SoftwareSerial.h>
#include "DShot.h"
#include "SCSCL.h"

#include "servo.h"
#include "control.h"

#define MOTOR_POLES 14
#define TOP_MOTOR_PIN 32
#define BOT_MOTOR_PIN 33
hw_timer_t *motor_timer = NULL;
dshot_t top_motor;
dshot_t bot_motor;

#define TOP_MOTOR_TELE_RX_PIN 25
#define BOT_MOTOR_TELE_RX_PIN 26
hw_timer_t *motor_tele_timer = NULL;
SoftwareSerial top_motor_tele;
SoftwareSerial bot_motor_tele;
uint16_t top_telemetrie[5];
uint16_t bot_telemetrie[5];

#define TOP_SERVO_ID 1
#define BOT_SERVO_ID 2
#define SERVO_RX_PIN 25
#define SERVO_TX_PIN 27
HardwareSerial p_serial(2);
SCSCL sc(0);

hw_timer_t *display_timer = NULL;

void IRAM_ATTR onTeleTimer()
{
	// dshotReceiveTelemetry(&top_motor, top_telemetrie);
	// dshotReceiveTelemetry(&bot_motor, bot_telemetrie);
}

void IRAM_ATTR onMotorTimer()
{
	dshotOutput(&top_motor);
	dshotOutput(&bot_motor);
}

void IRAM_ATTR display()
{
	// Serial.println("----------");
	// Serial.printf("top:\n %dc, %fv, %fA, %drpm\n",
	// 			  top_telemetrie[0],
	// 			  top_telemetrie[1] / 100.0,
	// 			  top_telemetrie[2] / 10.0,
	// 			  top_telemetrie[4] * 100 / (MOTOR_POLES / 2));

	// Serial.printf("\nbot:\n %dc, %fv, %fA, %drpm\n",
	// 			  bot_telemetrie[0],
	// 			  bot_telemetrie[1] / 100.0,
	// 			  bot_telemetrie[2] / 10.0,
	// 			  bot_telemetrie[4] * 100 / (MOTOR_POLES / 2));
	// Serial.println("----------");
	
	// servoDetails(sc, TOP_SERVO_ID, Serial);
	// servoDetails(sc, BOT_SERVO_ID, Serial);
}

void setup()
{
	Serial.begin(115200);
	Serial.setTimeout(5000);
	Serial.println("init starting");

	// Servo init
	p_serial.begin(1000000, SERIAL_8N1, 25, 27);
	sc.pSerial = &p_serial;

	// Motor telemetry init
	// top_motor_tele.begin(115200, SWSERIAL_8N1, TOP_MOTOR_TELE_RX_PIN, TOP_MOTOR_TELE_RX_PIN, false, 256);
	// top_motor_tele.enableIntTx(false);
	// top_motor_tele.enableTx(false);
	// bot_motor_tele.begin(115200, SWSERIAL_8N1, BOT_MOTOR_TELE_RX_PIN, BOT_MOTOR_TELE_RX_PIN, false, 256);
	// bot_motor_tele.enableIntTx(false);
	// bot_motor_tele.enableTx(false);

	// Motors init
	dshotCreateMotor(&top_motor, TOP_MOTOR_PIN, &top_motor_tele);
	dshotCreateMotor(&bot_motor, BOT_MOTOR_PIN, &bot_motor_tele);

	// Motor timer init
	motor_timer = timerBegin(0, 80, true);
	timerAttachInterrupt(motor_timer, &onMotorTimer, true);
	timerAlarmWrite(motor_timer, 1000, true); // 1ms
	timerAlarmEnable(motor_timer);

	// Motor telemetry timer init
	motor_tele_timer = timerBegin(2, 80, true);
	timerAttachInterrupt(motor_tele_timer, &onTeleTimer, true);
	timerAlarmWrite(motor_tele_timer, 40000, true); // 20ms
	timerAlarmEnable(motor_tele_timer);

	// ESC init
	vTaskDelay(500 / portTICK_PERIOD_MS);
	dshotSetThrottle(&top_motor, 0);
	dshotSetThrottle(&bot_motor, 0);

	// Display timer init
	display_timer = timerBegin(3, 80, true);
	timerAttachInterrupt(display_timer, &display, true);
	timerAlarmWrite(display_timer, 1000000, true); // 1000ms
	timerAlarmEnable(display_timer);
}

void loop()
{
	controlPrintPrompt(Serial);

	int input = Serial.parseInt();

	switch (input)
	{
	case CONTROL_MOTOR_STOP:
	{
		Serial.println("stop");
		dshotSetThrottle(&top_motor, 0);
		dshotSetThrottle(&bot_motor, 0);
		break;
	}

	case 1:
	{
		Serial.println("10% speed");
		dshotSetThrottle(&top_motor, 200);
		dshotSetThrottle(&bot_motor, 200);
		break;
	}

	case 2:
	{
		Serial.println("20% speed");
		dshotSetThrottle(&top_motor, 400);
		dshotSetThrottle(&bot_motor, 400);
		break;
	}

	case 3:
	{
		Serial.println("30% speed");
		dshotSetThrottle(&top_motor, 600);
		dshotSetThrottle(&bot_motor, 600);
		break;

	}

	case CONTROL_MOTOR_CUSTOM_SPEED:
	{
		Serial.println("Custom speed");
		int top_rpm = Serial.parseInt();
		int bot_rpm = Serial.parseInt();

		Serial.printf("Speeding up to: %d %d\n", top_rpm, bot_rpm);
		
		dshotSetThrottle(&top_motor, top_rpm);
		dshotSetThrottle(&bot_motor, bot_rpm);
		break;
	}

	case CONTROL_SERVO_ARM:
	{
		Serial.println("Arm");
		servoArmBall(sc, TOP_SERVO_ID, BOT_SERVO_ID);
		vTaskDelay(2000 / portTICK_PERIOD_MS);
		break;
	}

	case CONTROL_SERVO_PUSH:
	{
		Serial.println("Push and Arm");
		servoLoadBall(sc, TOP_SERVO_ID, BOT_SERVO_ID);
		vTaskDelay(500 / portTICK_PERIOD_MS);

		servoPushBall(sc, TOP_SERVO_ID, BOT_SERVO_ID);
		vTaskDelay(800 / portTICK_PERIOD_MS);

		servoArmBall(sc, TOP_SERVO_ID, BOT_SERVO_ID);
		break;
	}
	
	default:
		break;
	}
}

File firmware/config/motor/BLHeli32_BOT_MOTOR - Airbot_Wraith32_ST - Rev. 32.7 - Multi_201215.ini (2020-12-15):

[ESC0]
Eep_Name=BOT_MOTOR
Eep_ESC_Layout=Airbot_Wraith32_ST
Eep_ESC_Mode=2
Eep_FW_Main_Revision=32
Eep_FW_Sub_Revision=70
Eep_Layout_Revision=44
Eep_Pgm_Direction=1
Eep_Pgm_Rampup_Pwr=100
Eep_Pgm_Pwm_Freq=24
Eep_Pgm_Comm_Timing=0
Eep_Pgm_Demag_Comp=2
Eep_Pgm_Ppm_Min_Throttle=900
Eep_Pgm_Ppm_Center_Throttle=1500
Eep_Pgm_Ppm_Max_Throttle=2100
Eep_Pgm_Enable_Throttle_Cal=1
Eep_Pgm_Temp_Prot_Enable=120
Eep_Pgm_Volt_Prot=8
Eep_Pgm_Curr_Prot=25
Eep_Pgm_Enable_Power_Prot=1
Eep_Pgm_Brake_On_Stop=0
Eep_Pgm_Beep_Strength=20
Eep_Pgm_Beacon_Strength=80
Eep_Pgm_Beacon_Delay=600
Eep_Pgm_LED_Control=63
Eep_Pgm_Max_Acceleration=100
Eep_Pgm_Nondamped_Mode=1
Eep_Pgm_Curr_Sense_Cal=100
Eep_Note_Config=255
Eep_Pgm_Sine_Mode=1
Eep_Pgm_Auto_Tlm_Mode=1
Eep_Pgm_Stall_Prot=0
Eep_Hw_Voltage_Sense_Capable=0
Eep_Hw_Current_Sense_Capable=0
Eep_Hw_LED_Capable_0=3
Eep_Hw_LED_Capable_1=2
Eep_Hw_LED_Capable_2=1
Eep_Hw_LED_Capable_3=0
Eep_Hw_Pwm_Freq_Min=255
Eep_Hw_Pwm_Freq_Max=255
Eep_Nondamped_Capable=1
Eep_Note_Array=

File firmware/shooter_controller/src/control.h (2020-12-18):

#include <Arduino.h>

#define CONTROL_MOTOR_STOP 7
#define CONTROL_MOTOR_CUSTOM_SPEED 4
#define CONTROL_SERVO_ARM 5
#define CONTROL_SERVO_PUSH 6

void controlPrintPrompt(HardwareSerial serial);

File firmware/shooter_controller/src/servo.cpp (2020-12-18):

#include "servo.h"

bool servoHealthchecks(SCSCL sc, int id_0, int id_1)
{
    return sc.ReadTemper(id_0) < SAFE_TEMP_MAX && sc.ReadTemper(id_1) < SAFE_TEMP_MAX;
}

void servoDetails(SCSCL sc, int id, HardwareSerial serial)
{
    serial.printf("===\nID %d\n", id);
    serial.printf("pos: %d\n", sc.ReadPos(id));
    serial.printf("speed: %d\n", sc.ReadSpeed(id));
    serial.printf("temp: %dc\n", sc.ReadTemper(id));
    serial.printf("volt: %fv\n", sc.ReadVoltage(id) / 10.0);
    serial.println("---");
}

void servoMoveBothTo(SCSCL sc, int id_0, int id_1, int pos_0, int pos_1)
{
    u8 id[2];
    u16 pos[2];
    u16 times[2];

    id[0] = id_0;
    id[1] = id_1;
    pos[0] = pos_0;
    pos[1] = pos_1;
    times[0] = 10;
    times[1] = 10;

    sc.SyncWritePos(id, 2, pos, times, NULL);
}

void servoMoveTo(SCSCL sc, int id, int pos)
{
    sc.WritePos(id, pos, 10);
}

void servoEnableTorque(SCSCL sc, int id, bool enable)
{
    sc.EnableTorque(id, enable);
}

void servoArmBall(SCSCL sc, int id_0, int id_1)
{
    int id_0_pos = 1680;
    int id_1_pos = 2380;

    servoMoveBothTo(sc, id_0, id_1, id_0_pos, id_1_pos);
}

void servoLoadBall(SCSCL sc, int id_0, int id_1)
{
    int id_0_pos = 1230;
    int id_1_pos = 2855;

    servoMoveBothTo(sc, id_0, id_1, id_0_pos, id_1_pos);
}

void servoPushBall(SCSCL sc, int id_0, int id_1)
{
    int id_0_pos = 2930;
    int id_1_pos = 1160;

    servoMoveBothTo(sc, id_0, id_1, id_0_pos, id_1_pos);
}

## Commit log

2020-11-19 Add models
    [BOM.xlsx, Bottom Plate.dwg, Front Mount.stl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]
2020-11-30 Add working esc control for upper motor
2020-11-30 Add motor control for both motors
2020-12-03 Add encoder support
2020-12-03 Update BOM
    [BOM.xlsx]
2020-12-08 Reorganize directory
    [Bottom Plate.dwg, Front Mount.stl, Left Mount.stl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]
2020-12-10 Add 3D printed parts
    [actuator encoder cover.stl, actuator housing.stl, actuator magnet cover.stl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]
2020-12-10 Add tennis shooter 3D model
    [Bottom Plate.dwg, Front Mount.stl, Left Mount.stl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]
2020-12-10 Update accurate BOM
    [BOM.xlsx]
2020-12-10 Add tennisbot v1 urdf model
    [base_link.STL, bot_trigger_link.STL, bot_wheel_link.STL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]
2020-12-11 Add init procedure for encoders
2020-12-11 Add init procedure for servos
2020-12-11 Add scs servo header file
2020-12-15 Add esc configs
2020-12-15 Update esc firmware to 32.7
2020-12-18 Add working servo control, control interface
